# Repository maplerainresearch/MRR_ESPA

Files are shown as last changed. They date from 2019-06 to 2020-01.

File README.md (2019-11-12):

# MRR ESPA
## A basic 3D printer control board based on ESP32

This is a bare-minimum 3D printer control board based on the ESP32 microcontroller, which comes with built-in WiFi and BlueTooth.

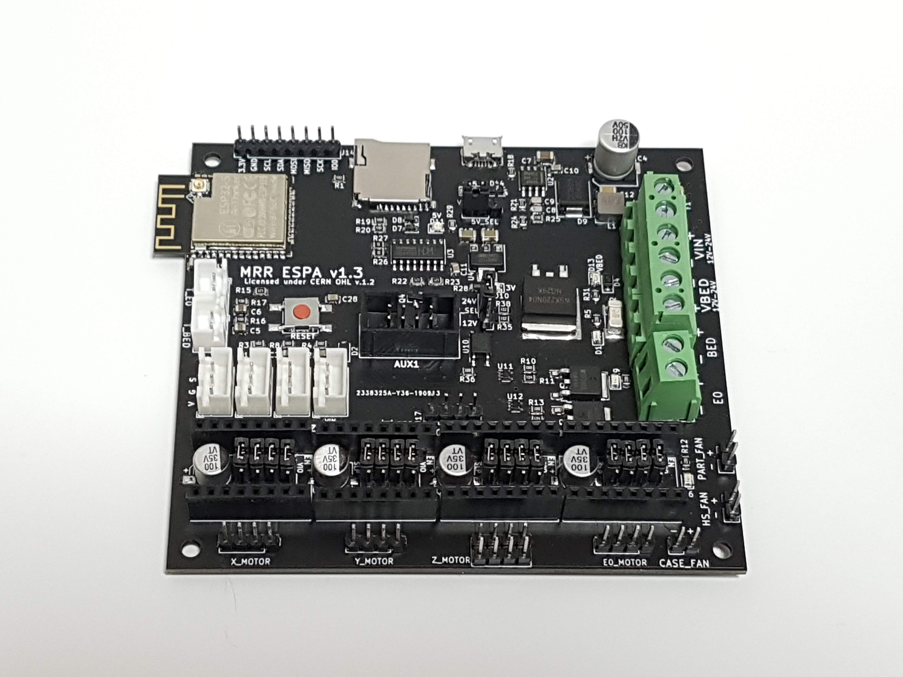
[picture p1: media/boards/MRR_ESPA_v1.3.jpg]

Current version: v1.3

Get a pre-launch version at our [store](https://www.maplerain.com/en/products).

Facebook [page](https://www.facebook.com/mrrespx/) <br>
Facebook [group](https://www.facebook.com/groups/mrr.espx.users/) (for discussions, etc.)

## Features:
- Able to use up to 4 stepper drivers: X, Y, Z, and E0
- 12V to 24V input power supply
- Separate power supply for the heat bed
- X, Y, and Z min endstops
- Allows the use of a Z-axis probe, such as an inductive sensor, running on the input supply voltage (12V to 24V)
- AUX1 connector for use with an external host, such as the closed-source MKS TFT32 (**Untested!!**)
- Physical size of 99.5mm by 90.5mm. Mounting holes are 3.5mm in diameter, with centers 4mm from the edges.
- "RESET" button can be used to reset the board.

(http://www.youtube.com/watch?v=s4IRmG6ibc4 "Basic features")

(http://www.youtube.com/watch?v=E-ERUolL-Bw "Printing via ESP3D webUI")

Check out the [Kickstarter page.](https://www.kickstarter.com/projects/maplerainresearch/mrr-espa)

# Firmware

Marlin 2.0 has added support for ESP32. This board was based on the initial pins definition used. <br>
In addition, [Luc](https://github.com/luc-github) has been working on a Marlin fork which incorporates part of his ESP3D webUI into Marlin itself.

## Flashing firmware

- You should be able to flash firmware through the USB port. Depending on your operating system, you may need to install drivers for the CH340. Please use Google or another search engine to find the right CH340 driver for your operating system.
- To flash firmware by directly connecting to TX/RX pins, you will need to connect IO0 to GND, then reboot (press "BOOT" button) to enter flash mode. After flashing the firmware, disconnect IO0 from GND, and press "BOOT" button again to reboot into normal mode.
- Use a baud rate of 115200.
- Once the firmware has been flashed for the first time, further updates can be flashed via OTA.

# Jumpers

- 5V_SEL: Connect to VIN for normal operation; only short (close) this jumper to VUSB if you need to power the board via USB. Note: Powering the board with both PSU and USB may cause unstable operation during heating.
- PWR_SEL: Connect the middle pin PWR_SEL to pin labeled "12V" if using 12V; connect PWR_SEL to pin labeled "24V" if using 24V.
- Stepper driver jumpers:
  - MS1: VIO to set high; SPI if using TMC SPI mode
  - MS2: VIO to set high; SPI if using TMC SPI mode
  - MS3: VIO to set high; SPI if using TMC SPI mode
  - RST: SLP if using A4988/DRV8825; SPI if using TMC SPI mode

# Pins

See separate PIN_DEF.txt file.

# License
Released under CERN Open Hardware Licence v1.2. See LICENSE.txt for details.

## Warning

- This product uses high currents which may cause fires. Use with caution.
- Do not use input voltages higher than 24V. Input current must not exceed 15A.
- Do not attempt to use more than 15A for the heated bed. While the MOSFET is capable of such currents, the connectors are not. If you need more than 15A, use an external MOSFET. In any case, it is highly recommended to use an external MOSFET for the heated bed to avoid drawing high currents through this product.
- If using a current of more than 10A for the heated bed, it is highly recommended to provide active cooling for the board as the MOSFET and adjacent areas can get very hot due to the high current.
- The underside of the board has PCB traces which are exposed for better cooling. These traces may be carrying high currents and can get very hot. DO NOT touch them, and DO NOT allow these traces to come into contact with metal or other conductive materials.
- Do not attempt to use more than 5A for the hot end. While the MOSFET is capable of such currents, the connectors are not. If you need more than 5A, use an external MOSFET.
- Do not reverse polarity.
- The breakout and endstop pins are rated for 3.3V, which is the voltage the ESP32 operates at. Attempting to feed inputs above 3.3V to these pins may damage the board.
- It is recommended to power the board only via USB (i.e. turn off PSU power supply) when flashing the board.

## Disclaimer

This product is provided as-is. While care has been taken to design a safe product, it is the user's responsibility to make sure precautions are taken to prevent damage or injury when using this product. This includes adhering to all warnings provided. By using this product, the user accepts responsibility to bear all liabilities from any damage or injury arising from the use of this product.

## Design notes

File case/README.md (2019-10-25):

# Cases for MRR ESPA

There are three versions:
1. Basic: Skeleton version, with a simple base, and a top that allows a 40mm fan to be fitted. Standoffs (at least 25mm; more if using stepper drivers with higher heat sinks) are needed.
2. Small: A small, almost enclosed case with a top that allows a 80mm fan to be fitted.
3. Normal: A slightly larger enclosed case, with two types of tops (either a 80mm fan, or two 40mm fans).

There are also covers for 40mm and 80mm fans.

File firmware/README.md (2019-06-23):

This directory contains ZIP files of firmware which works with the MRR ESP 3DP board.

MRR ESP 3DP board works with the [Marlin fork](https://github.com/luc-github/Marlin) currently under development by [Luc](https://github.com/luc-github). This fork provides WiFi support as well as a web UI based on Luc's [ESP3D](https://github.com/luc-github/ESP3D). Snapshots of the repo will be posted here. You can download the ZIP file, unpack it, and edit the Configuration.h and Configuration_adv.h to suit the size of your printer, drivers, etc. If you are using TMC2130 drivers in SPI mode, you will also need to edit pins_ESP32.h to specify the CS pins for the drivers. The fork has been tested to compile under Arduino IDE 1.8.5 using Arduino-ESP32 core v1.0.0 (stable release).

If you are using an external host such as the MKS TFT32 or Octoprint, you can also use vanilla Marlin 2.0, which has ESP32 support. However, this does not come with WiFi nor a web UI.

When flashing firmware, use a baud rate of 115200.

Default admin name and password:<br>
User: admin<br>
Password: admin<br>
<br>
Default general user name and password:<br>
User: user<br>
Password: user<br>

Default mDNS name: **marlinesp**, which can be accessed on web browsers by going to `http://marlinesp.local/`

For more about the web UI, see Luc's [ESP3D-WEBUI](https://github.com/luc-github/ESP3D-WEBUI) repository.

# Instructions for flashing firmware

The firmware is built on the Arduino framework with the ESP32 core from Espressif. If you have experience building and flashing firmware using the Arduino-ESP32 core, you probably do not need this guide and can easily flash the firmware using your usual method. Otherwise, you can follow the following to flash the firmware.

1. First, you need Arduino IDE installed on your computer (Windows, Mac, or Linux). Go to [Arduino IDE's download page](https://www.arduino.cc/en/main/software) to download the version of the IDE for your computer. Arduino IDE's installation guide can be found [here](https://www.arduino.cc/en/Guide/HomePage).

2. Once Arduino IDE has been installed, follow the instructions [here](https://github.com/espressif/arduino-esp32/blob/master/docs/arduino-ide/boards_manager.md) to install the ESP32 core for Arduino IDE. It is recommended to install the stable release.

3. Download or clone the [Marlin fork](https://github.com/luc-github/Marlin) currently under development by [Luc](https://github.com/luc-github).

4. Connect the board to your computer via USB cable.

5. Launch Arduino IDE, and open the sketch for the firmware. This file is named `Marlin.ino` and can be found in the downloaded firmware's `Marlin` subdirectory.

6. In the IDE's menu, go to `Tools`, then `Board`, and choose `ESP32 Dev Module` which is the generic ESP32 module. Then, under `Tools`, `Port`, choose the COM port that your board is connected to. For upload speed, go to `Tools`, `Upload speed`, and set to `115200`.

7. Edit the `Configuration.h` and `Configuration_adv.h` files to define the size of your printer, endstops, and other settings. See the section below for some basic settings which need to be changed.

8. Click on the "Upload" icon of the IDE to compile the firmware and flash it onto the board. This will take quite a while.

9. Once the firmware has been flashed onto the board, you can open the IDE's serial monitor (by pressing Ctrl+Shift+M, or from the menu via `Tools`, then `Serial monitor`) to make sure the firmware has been flashed properly. Enter `M503` into the serial monitor and you should get a response from the board giving the current settings such as steps/mm and PID values.

10. Via the serial monitor, you can configure your WiFi settings. See the section below on how to do so. You can also set up WiFi using a web browser (see relevant section below).

# Instructions for setting up WiFi via terminal

Once the firmware has been flashed for the first time, there is a need to do an initial setup for the WiFi settings.<br>
In Arduino IDE, open up the serial monitor to connect to the board. You can also use any other terminal program to open the COM port that the board is connected to. Then, type in the following commands 1 to 3 to set up the board in station mode (connect to an existing WiFi router). To set up in AP mode, use commands 1, 4, and 5.

1. `M586 P0 S1 R80`<br>
Enable HTTP on port 80.<br>
Replace `R80` with `Rxx` (xx is the port number) to run the HTTP server on another port.

2. `M587 S"abcd" P"12345" I192.168.0.25`<br>
WiFi settings; the above will connect to a SSID of `abcd` with password `12345` and attempt to use a static address of `192.168.0.25` (note: the quotation marks are necessary for SSID and password). Change `abcd`, `12345`, and `192.168.0.25` to your own values. `I192.168.0.25` can be left out if a static address is not needed.

3. `M588 S1 P1`<br>
This will start up WiFi in station mode, using the settings set by `M587`. The IP address of the webserver will be displayed in the terminal. Use this IP address to connect to the webserver. For example, going to `http://192.168.0.25:80/` on your web browser following the above example.

4. `M589 S"ESP32" P"12345" I192.168.10.1`<br>
WiFi settings; the above will create an access point with SSID of `ESP32` and password `12345`, and the webserver will be on IP address `192.168.10.1` (note: the quotation marks are necessary for SSID and password). WPA2 security will be used by default.

5. `M588 S2 P1`<br>
This will start up WiFi in AP mode, using the settings set by `M589`.

# Instructions for setting up WiFi via web browser

To be completed.

# Uploading webUI

When you first go to the webUI address (if you have mDNS, this should be http://marlinesp.local/ by default), you will be asked to upload the webUI files. Click on "Choose files", select `index.html.gz`, then upload. Then, refresh your browser page; the webUI should load. A copy of `index.html.gz` can be found in the firmware directory, under `<firmware directory>/Marlin/data/`.<br>

If you have the [Arduino ESP32 filesystem uploader](https://github.com/me-no-dev/arduino-esp32fs-plugin), you can also choose to upload the required files from Arduino IDE. After flashing the firmware, go to `Tools`, then choose `ESP32 Sketch Data Upload`.

# Common settings which need to be changed in Marlin

The following are some common settings which need to be changed in Marlin to configure the firmware for your specific printer.<br>

In `Configuration.h`:
To be completed.<br>

In `Configuration_adv.h`:
To be completed.<br>

In `Marlin\src\pins\pins_ESP32.h`:
The following lines need to be added in order for microSD card to work.<br>
```
#define MOSI_PIN           23
#define MISO_PIN           19
#define SCK_PIN            18
#define SS_PIN              5
#define SDSS                5
```

# Macros

The webUI (based on ESP3D) allows user-defined macros to be created. This allows "buttons" for custom commands (GCODE), such as buttons for babystepping.<br>

For example, to add a command to move to babystep Z by 0.01 downwards:
1. Create a text file with the gcode. In this case the gcode would be "M290 Z-0.01". Save it with a ".g" extension. In this case, it can be named `babyzdn.g`.
2. Upload that file to the ESP3D File System (Not to the SD card); this is the SPIFFS file system, where `index.html.gz` is stored.
3. Click on the macro editor button in the controls panel. click the plus icon to add a macro. Give it a name, select a color, set the target as ESP and enter the path to the gcode file you uploaded.
4. Click Save
(Example based on [GRBL_ESP32 wiki](https://github.com/bdring/Grbl_Esp32/wiki/ESP3D-Web-UI-for-Grbl_ESP32); GRBL_ESP32 is a fork of GRBL with luc-github's ESP3D webUI.)<br>

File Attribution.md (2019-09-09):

# Attribution

Schematics of the following boards were referenced in the design of MRR ESPA:
- [SMART RAMPS 1.42](https://reprap.org/wiki/SMART_RAMPS)
- [ESP32Controller](https://github.com/simon-jouet/ESP32Controller)
- [STEVAL-3DP001V1](https://www.st.com/en/evaluation-tools/steval-3dp001v1.html)
- [Duet 3D Printer Controller](https://github.com/T3P3/Duet)
- [Smoothieboard](https://github.com/Smoothieware/Smoothieboard)
- [Arduino UNO R3](https://www.arduino.cc/en/uploads/Main/Arduino_Uno_Rev3-schematic.pdf)
- [Little-Driver](https://github.com/Digital-Sqrt/Little-Driver)

Software:
- [Custom Marlin fork](https://github.com/luc-github/Marlin) by luc-github
- [ESP3D-WEBUI](https://github.com/luc-github/ESP3D-WEBUI)
- [Marlin firmware](https://github.com/MarlinFirmware/Marlin)

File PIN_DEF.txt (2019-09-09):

Pin Definitions for MRR ESPE
----------------------------

ESP32 pins
0: unused (IO0; must not be pulled low for normal bootup)
1: TX
2: HEATER_0_PIN
3: RX
4: HEATER_BED_PIN
5: SS_PIN (SDSS)
12: Z_DIR_PIN
13: FAN_PIN
14: Z_STEP_PIN
15: Z_MIN_PIN
16: E0_STEP_PIN
17: E0_DIR_PIN
18: SCK_PIN
19: MISO_PIN
21: unused (SDA)
22: unused (SCL)
23: MOSI_PIN
25: X_ENABLE_PIN (shared with Y, Z, and E0)
26: X_DIR_PIN
27: X_STEP_PIN
32: Y_DIR_PIN
33: Y_STEP_PIN
34: X_MIN_PIN
35: Y_MIN_PIN
36 (VP): TEMP_0_PIN
39 (VN): TEMP_BED_PIN

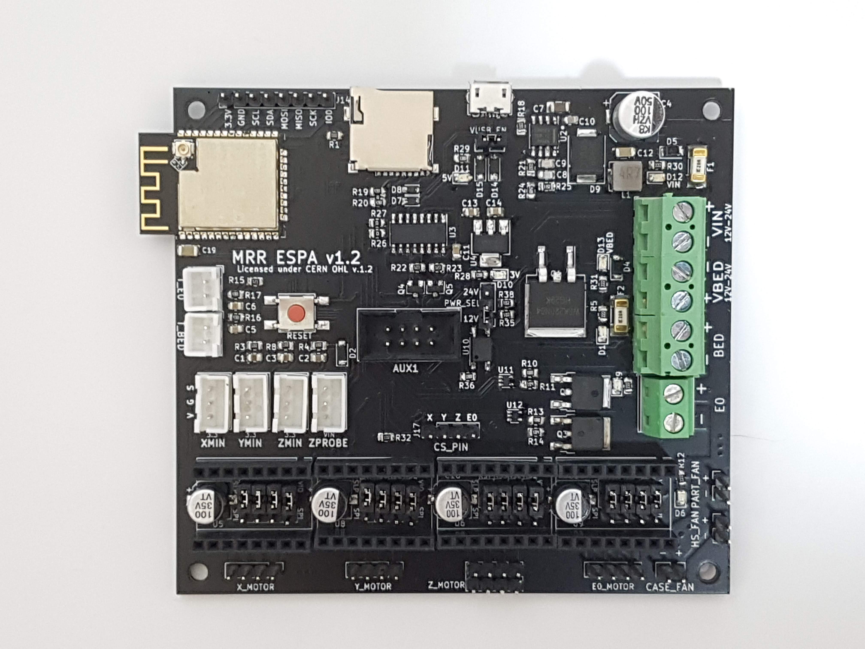
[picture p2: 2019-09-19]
media/ESPA board overview.jpg

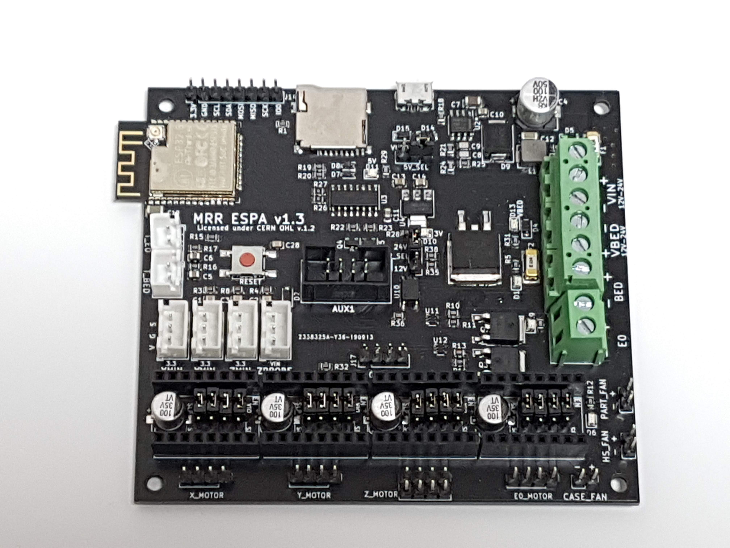
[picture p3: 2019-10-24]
media/MRR ESPA v1.3 board overview.jpg

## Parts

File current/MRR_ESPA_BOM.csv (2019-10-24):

Reference | Value | Footprint | Datasheet | LCSC Part Number | Manufacturer | Mfg part no.
U1 | ESP32-WROOM-32D | RF_Module:ESP32-WROOM-32 | https://www.espressif.com/sites/default/files/documentation/esp32-wroom-32d_esp32-wroom-32u_datasheet_en.pdf | C95209 | Espressif Systems | ESP32-WROOM-32
J9 | PWR_IN | TerminalBlock_Phoenix:TerminalBlock_Phoenix_MKDS-3-4-5.08_1x04_P5.08mm_Horizontal | ~ | C90087 | Phoenix Contact | MKDS3/4-5.08
F1 | 15A 2410 | projfp:Littelfuse_0451 | Bel 0679H9150-01 | C44480 | Littelfuse | 0451015.MRL
F2 | 30A 3912 | projfp:Littelfuse_456 | Bel 0678H9300-02 | C187558 | Littelfuse | 0456030.ER
D4 | 1N4007W | projfp:D_SOD-123F | http://www.vishay.com/docs/88503/1n4001.pdf | C108803 | Shandong Jingdao Microelectronics | 1N4007W
D5 | 1N4007W | projfp:D_SOD-123F | http://www.vishay.com/docs/88503/1n4001.pdf | C108803 | Shandong Jingdao Microelectronics | 1N4007W
U2 | TPS54340DDA | Package_SO:TI_SO-PowerPAD-8_ThermalVias | http://www.ti.com/lit/ds/symlink/tps54340.pdf | C45886 | Texas Instruments | TPS54340DDAR
C10 | 100nF50V | Capacitor_SMD:C_0805_2012Metric | ~ | C161260 | Murata Electronics | GCM21BR71H104KA37L
C7 | 4.7uF50V | Capacitor_SMD:C_1206_3216Metric | ~ | C307575 | Samsung Electro-Mechanics | CL31B475KBHNFNE
C4 | 100uF50V | Capacitor_SMD:CP_Elec_8x10 | ~ | C176665 | Lelon | VEJ101M1HTR-0810
L1 | 4.7uH4.5A | projfp:SMMS0530 | ~ | C181722 | Shun Xiang Nuo Elec | SMMS0530-4R7M
D9 | B540C-13-F | projfp:D_SMC | ~ | C72264 | Diodes Incorporated | B540C-13-F
R24 | 60.4K | Resistor_SMD:R_0805_2012Metric | ~ | C273994 | YAGEO | RC0805FR-0760K4L
R25 | 11.5K | Resistor_SMD:R_0805_2012Metric | ~ | C17418 | Uniroyal Elec | 0805W8F1152T5E
C12 | 47uF16V | Capacitor_SMD:C_1206_3216Metric | ~ | C92821 | Taiyo Yuden | LMK316BJ476ML-T
C8 | 820pF50V | Capacitor_SMD:C_0805_2012Metric | ~ | C152862 | Walsin Tech Corp | 0805B821K500CT
R21 | 23.7K | Resistor_SMD:R_0805_2012Metric | ~ | C170848 | Walsin Tech Corp | WR08X2372FTL
C9 | 56pF50V | Capacitor_SMD:C_0805_2012Metric | ~ | C296102 | Walsin Tech Corp | 0805N560J500CT
R18 | 73.2K | Resistor_SMD:R_0805_2012Metric | ~ | C170958 | Walsin Tech Corp | WR08X7322FTL
U4 | AMS1117-3.3 | Package_TO_SOT_SMD:SOT-223-3_TabPin2 | http://www.advanced-monolithic.com/pdf/ds1117.pdf | C6186 | Advanced Monolithic Systems | AMS1117-3.3
C14 | 47uF6.3V | Capacitor_SMD:C_0805_2012Metric | ~ | C87159 | Taiyo Yuden | JMK212BJ476MG-T
C13 | 47uF6.3V | Capacitor_SMD:C_0805_2012Metric | ~ | C87159 | Taiyo Yuden | JMK212BJ476MG-T
R28 | 220R | Resistor_SMD:R_0805_2012Metric | ~ | C17557 | Uniroyal Elec | 0805W8F2200T5E
D10 | LED_3V | projfp:LED_0805 | ~ | C73548 | Everlight Elec | 17-21SYGC/S530-E2/TR8
R29 | 330R | Resistor_SMD:R_0805_2012Metric | ~ | C17630 | Uniroyal Elec | 0805W8F3300T5E
R30 | 2.2K | Resistor_SMD:R_0805_2012Metric | ~ | C17520 | Uniroyal Elec | 0805W8F2201T5E
R31 | 2.2K | Resistor_SMD:R_0805_2012Metric | ~ | C17520 | Uniroyal Elec | 0805W8F2201T5E
D11 | LED_5V | projfp:LED_0805 | ~ | C73548 | Everlight Elec | 17-21SYGC/S530-E2/TR8
D12 | LED_VIN | projfp:LED_0805 | ~ | C72035 | Everlight Elec | 17-21/BHC-XL2M2TY/3T
D13 | LED_VBED | projfp:LED_0805 | ~ | C72035 | Everlight Elec | 17-21/BHC-XL2M2TY/3T
R26 | 0R | Resistor_SMD:R_0805_2012Metric | ~ | C17477 | Uniroyal Elec | 0805W8F0000T5E
R27 | 0R | Resistor_SMD:R_0805_2012Metric | ~ | C17477 | Uniroyal Elec | 0805W8F0000T5E
C11 | 10nF50V | Capacitor_SMD:C_0805_2012Metric | ~ | C52278 | Guangdong Fenghua Advanced Tech | 0805B103K500NT
J16 | USB_B_Micro | Connector_USB:USB_Micro-B_Molex-105017-0001 | ~ | C136000 | MOLEX | 105017-0001
D7 | PESD5V0S1BA | projfp:D_SOD-323 | ~ | C19224 | Nexperia | PESD5V0S1BA,115
D8 | PESD5V0S1BA | projfp:D_SOD-323 | ~ | C19224 | Nexperia | PESD5V0S1BA,115
Q4 | S9014 | Package_TO_SOT_SMD:SOT-23 | http://www.onsemi.com/pub_link/Collateral/2N3055-D.PDF | C181164 | Guangdong Hottech | S9014
Q5 | S9014 | Package_TO_SOT_SMD:SOT-23 | http://www.onsemi.com/pub_link/Collateral/2N3055-D.PDF | C181164 | Guangdong Hottech | S9014
R22 | 12K | Resistor_SMD:R_0805_2012Metric | ~ | C17444 | Uniroyal Elec | 0805W8F1202T5E
R23 | 12K | Resistor_SMD:R_0805_2012Metric | ~ | C17444 | Uniroyal Elec | 0805W8F1202T5E
Q1 | WSK220N04 | Package_TO_SOT_SMD:TO-263-2 | ~ | C148446 | Winsok Semicon | WSK220N04
Q2 | WSF3085 | Package_TO_SOT_SMD:TO-252-2 | ~ | C148428 | Winsok Semicon | WSF3085
Q3 | WSF3038 | Package_TO_SOT_SMD:TO-252-2 | ~ | C148426 | Winsok Semicon | WSF3038
R5 | 2.2K | Resistor_SMD:R_0805_2012Metric | ~ | C17520 | Uniroyal Elec | 0805W8F2201T5E
D1 | LED_BED | projfp:LED_0805 | ~ | C72037 | Everlight Elec | 17-21SURC/S530-A3/TR8
J3 | BED | TerminalBlock_Phoenix:TerminalBlock_Phoenix_MKDS-3-2-5.08_1x02_P5.08mm_Horizontal | ~ | C89120 | Phoenix Contact | MKDS3/2-5.08
R9 | 2.2K | Resistor_SMD:R_0805_2012Metric | ~ | C17520 | Uniroyal Elec | 0805W8F2201T5E
J7 | E0 | TerminalBlock_Phoenix:TerminalBlock_Phoenix_MKDS-1,5-2-5.08_1x02_P5.08mm_Horizontal | ~ | C91153 | Phoenix Contact | MKDSN1.5/2-5.08
R10 | 10R | Resistor_SMD:R_0805_2012Metric | ~ | C17415 | Uniroyal Elec | 0805W8F100JT5E
R11 | 100K | Resistor_SMD:R_0805_2012Metric | ~ | C149504 | Uniroyal Elec | 0805W8F1003T5E
R12 | 2.2K | Resistor_SMD:R_0805_2012Metric | ~ | C17520 | Uniroyal Elec | 0805W8F2201T5E
R13 | 10R | Resistor_SMD:R_0805_2012Metric | ~ | C17415 | Uniroyal Elec | 0805W8F100JT5E
R14 | 100K | Resistor_SMD:R_0805_2012Metric | ~ | C149504 | Uniroyal Elec | 0805W8F1003T5E
J10 | PART_FAN | Connector_PinHeader_2.54mm:PinHeader_1x02_P2.54mm_Vertical | ~ | C124375 | Shenzhen Cankemeng | C124375
U8 | Pololu_board | Module:Pololu_Breakout-16_15.2x20.3mm |  | C27438 | Boom Precision Elec | x2
U5 | Pololu_board | Module:Pololu_Breakout-16_15.2x20.3mm |  | C27438 | Boom Precision Elec | x2
J21 | X_MOTOR | Connector_PinHeader_2.54mm:PinHeader_1x04_P2.54mm_Vertical | ~ | C124378 | Shenzhen Cankemeng | C124378
C15 | 100uF35V | Capacitor_SMD:CP_Elec_6.3x7.7 | ~ | C97811 | Semtech | CS1V101M-CRE77
U6 | Pololu_board | Module:Pololu_Breakout-16_15.2x20.3mm |  | C27438 | Boom Precision Elec | x2
U9 | Pololu_board | Module:Pololu_Breakout-16_15.2x20.3mm |  | C27438 | Boom Precision Elec | x2
R32 | 10K | Resistor_SMD:R_0805_2012Metric | ~ | C38522 | Uniroyal Elec | 0805W8F2201T5E
J11 | FAN_HEATSINK | Connector_PinHeader_2.54mm:PinHeader_1x02_P2.54mm_Vertical | ~ | C124375 | Shenzhen Cankemeng | C124375
C16 | 100uF35V | Capacitor_SMD:CP_Elec_6.3x7.7 | ~ | C97811 | Semtech | CS1V101M-CRE77
C17 | 100uF35V | Capacitor_SMD:CP_Elec_6.3x7.7 | ~ | C97811 | Semtech | CS1V101M-CRE77
C18 | 100uF35V | Capacitor_SMD:CP_Elec_6.3x7.7 | ~ | C97811 | Semtech | CS1V101M-CRE77
J23 | Y_MOTOR | Connector_PinHeader_2.54mm:PinHeader_1x04_P2.54mm_Vertical | ~ | C124378 | Shenzhen Cankemeng | C124378
J24 | E0_MOTOR | Connector_PinHeader_2.54mm:PinHeader_1x04_P2.54mm_Vertical | ~ | C124378 | Shenzhen Cankemeng | C124378
J22 | Z_MOTOR | Connector_PinHeader_2.54mm:PinHeader_2x04_P2.54mm_Vertical | ~ | C124386 | Shenzhen Cankemeng | C124386
D3 | LED_E0 | projfp:LED_0805 | ~ | C72037 | Everlight Elec | 17-21SURC/S530-A3/TR8
D6 | LED_FAN | projfp:LED_0805 | ~ | C72037 | Everlight Elec | 17-21SURC/S530-A3/TR8
J8 | FAN_CASE | Connector_PinHeader_2.54mm:PinHeader_1x02_P2.54mm_Vertical | ~ | C124375 | Shenzhen Cankemeng | C124375
J12 | T_BED | Connector_JST:JST_XH_B02B-XH-A_1x02_P2.50mm_Vertical | ~ | C158012 | JST Sales America | B2B-XH-A(LF)(SN)
R16 | 4.7K | Resistor_SMD:R_0805_2012Metric | ~ | C17673 | Uniroyal Elec | 0805W8F4701T5E
C5 | 22uF6.3V | Capacitor_SMD:C_0805_2012Metric | ~ | C5674 | Samsung Electro-Mechanics | CL21A226MQQNNNE
J13 | T_E0 | Connector_JST:JST_XH_B02B-XH-A_1x02_P2.50mm_Vertical | ~ | C158012 | JST Sales America | B2B-XH-A(LF)(SN)
R17 | 4.7K | Resistor_SMD:R_0805_2012Metric | ~ | C17673 | Uniroyal Elec | 0805W8F4701T5E
C6 | 22uF6.3V | Capacitor_SMD:C_0805_2012Metric | ~ | C5674 | Samsung Electro-Mechanics | CL21A226MQQNNNE
J1 | X_MIN | Connector_JST:JST_XH_B03B-XH-A_1x03_P2.50mm_Vertical | ~ | C144394 | JST Sales America | B3B-XH-A(LF)(SN)
R3 | 10K | Resistor_SMD:R_0805_2012Metric | ~ | C38522 | Uniroyal Elec | 0805W8F2201T5E
C1 | 100nF25V | Capacitor_SMD:C_0805_2012Metric | ~ | C128353 | Walsin Tech Corp | 0805B104K250
J5 | Y_MIN | Connector_JST:JST_XH_B03B-XH-A_1x03_P2.50mm_Vertical | ~ | C144394 | JST Sales America | B3B-XH-A(LF)(SN)
R8 | 10K | Resistor_SMD:R_0805_2012Metric | ~ | C38522 | Uniroyal Elec | 0805W8F2201T5E
C3 | 100nF25V | Capacitor_SMD:C_0805_2012Metric | ~ | C128353 | Walsin Tech Corp | 0805B104K250
J2 | Z_MIN | Connector_JST:JST_XH_B03B-XH-A_1x03_P2.50mm_Vertical | ~ | C144394 | JST Sales America | B3B-XH-A(LF)(SN)
R4 | 10K | Resistor_SMD:R_0805_2012Metric | ~ | C38522 | Uniroyal Elec | 0805W8F2201T5E
C2 | 100nF25V | Capacitor_SMD:C_0805_2012Metric | ~ | C128353 | Walsin Tech Corp | 0805B104K250
J6 | Z_PROBE | Connector_JST:JST_XH_B03B-XH-A_1x03_P2.50mm_Vertical | ~ | C144394 | JST Sales America | B3B-XH-A(LF)(SN)
D2 | 1N4148W | projfp:D_SOD-123 | https://www.vishay.com/docs/85748/1n4148w.pdf | C81598 | Semtech | 1N4148W
R15 | 12K | Resistor_SMD:R_0805_2012Metric | ~ | C17444 | Uniroyal Elec | 0805W8F1202T5E
SW1 | RESET | projfp:6x6mmTactileSwitch |  | C83206 | Korean Hroparts Elec | K2-6639SP-C4SC-04
J15 | AUX1 | Connector_IDC:IDC-Header_2x04_P2.54mm_Vertical | ~ | C9135 | Boom Precision Elec | C9135
J14 | I2C/SPI | Connector_PinHeader_2.54mm:PinHeader_1x08_P2.54mm_Vertical | ~ | C124381 | Shenzhen Cankemeng | C124381
R19 | 4.7K | Resistor_SMD:R_0805_2012Metric | ~ | C17673 | Uniroyal Elec | 0805W8F4701T5E
R20 | 4.7K | Resistor_SMD:R_0805_2012Metric | ~ | C17673 | Uniroyal Elec | 0805W8F4701T5E
H1 | MountingHole | MountingHole:MountingHole_3.2mm_M3_DIN965 | ~
H2 | MountingHole | MountingHole:MountingHole_3.2mm_M3_DIN965 | ~
H3 | MountingHole | MountingHole:MountingHole_3.2mm_M3_DIN965 | ~
H4 | MountingHole | MountingHole:MountingHole_3.2mm_M3_DIN965 | ~
JP1 | X_MS1 | Connector_PinHeader_2.54mm:PinHeader_1x03_P2.54mm_Vertical | ~ | C124376 | Shenzhen Cankemeng | C124376
JP5 | X_MS2 | Connector_PinHeader_2.54mm:PinHeader_1x03_P2.54mm_Vertical | ~ | C124376 | Shenzhen Cankemeng | C124376
JP9 | X_MS3 | Connector_PinHeader_2.54mm:PinHeader_1x03_P2.54mm_Vertical | ~ | C124376 | Shenzhen Cankemeng | C124376
JP13 | X_RST | Connector_PinHeader_2.54mm:PinHeader_1x03_P2.54mm_Vertical | ~ | C124376 | Shenzhen Cankemeng | C124376
JP2 | Y_MS1 | Connector_PinHeader_2.54mm:PinHeader_1x03_P2.54mm_Vertical | ~ | C124376 | Shenzhen Cankemeng | C124376
JP6 | Y_MS2 | Connector_PinHeader_2.54mm:PinHeader_1x03_P2.54mm_Vertical | ~ | C124376 | Shenzhen Cankemeng | C124376
JP10 | Y_MS3 | Connector_PinHeader_2.54mm:PinHeader_1x03_P2.54mm_Vertical | ~ | C124376 | Shenzhen Cankemeng | C124376
JP14 | Y_RST | Connector_PinHeader_2.54mm:PinHeader_1x03_P2.54mm_Vertical | ~ | C124376 | Shenzhen Cankemeng | C124376
JP3 | Z_MS1 | Connector_PinHeader_2.54mm:PinHeader_1x03_P2.54mm_Vertical | ~ | C124376 | Shenzhen Cankemeng | C124376
JP7 | Z_MS2 | Connector_PinHeader_2.54mm:PinHeader_1x03_P2.54mm_Vertical | ~ | C124376 | Shenzhen Cankemeng | C124376
JP11 | Z_MS3 | Connector_PinHeader_2.54mm:PinHeader_1x03_P2.54mm_Vertical | ~ | C124376 | Shenzhen Cankemeng | C124376
JP15 | Z_RST | Connector_PinHeader_2.54mm:PinHeader_1x03_P2.54mm_Vertical | ~ | C124376 | Shenzhen Cankemeng | C124376
JP4 | E0_MS1 | Connector_PinHeader_2.54mm:PinHeader_1x03_P2.54mm_Vertical | ~ | C124376 | Shenzhen Cankemeng | C124376
JP8 | E0_MS2 | Connector_PinHeader_2.54mm:PinHeader_1x03_P2.54mm_Vertical | ~ | C124376 | Shenzhen Cankemeng | C124376
JP12 | E0_MS3 | Connector_PinHeader_2.54mm:PinHeader_1x03_P2.54mm_Vertical | ~ | C124376 | Shenzhen Cankemeng | C124376
JP16 | E0_RST | Connector_PinHeader_2.54mm:PinHeader_1x03_P2.54mm_Vertical | ~ | C124376 | Shenzhen Cankemeng | C124376
U3 | CH340C | Package_SO:SOIC-16_3.9x9.9mm_P1.27mm | http://www.datasheet5.com/pdf-local-2195953 | C84681 | Jiangsu Qin Heng | CH340C
J4 | Micro_SD_Card_China | projfp:Conn_uSDcard |  | C111196 | SOFNG | TF-15×15
C19 | 100uF6.3V | Capacitor_SMD:C_1206_3216Metric | ~ | C15008 | Samsung Electro-Mechanics | CL31A107MQHNNNE
R38 | 1K | Resistor_SMD:R_0805_2012Metric | ~ | C17513 | Uniroyal Elec | 0805W8F1001T5E
R35 | 1K | Resistor_SMD:R_0805_2012Metric | ~ | C17513 | Uniroyal Elec | 0805W8F1001T5E
U10 | TLP182 | Package_SO:MFSOP6-4_4.4x3.6mm_P1.27mm | https://toshiba.semicon-storage.com/info/docget.jsp?did=11793&prodName=TLP184 | C96457 | TOSHIBA | TLP182(GB-TPL,E
U11 | 74LVC1G125 | Package_TO_SOT_SMD:SOT-353_SC-70-5 | http://www.ti.com/lit/sg/scyt129e/scyt129e.pdf | C12519 | Nexperia | 74LVC1G125GW,125
U12 | 74LVC1G125 | Package_TO_SOT_SMD:SOT-353_SC-70-5 | http://www.ti.com/lit/sg/scyt129e/scyt129e.pdf | C12519 | Nexperia | 74LVC1G125GW,125
R36 | 330R | Resistor_SMD:R_0805_2012Metric | ~ | C17630 | Uniroyal Elec | 0805W8F3300T5E
D14 | 1N5819W | Diode_SMD:D_SOD-123 | http://www.vishay.com/docs/88525/1n5817.pdf | C169540 | Shandong Jingdao Microelectronics | 1N5819W
D15 | 1N5819W | Diode_SMD:D_SOD-123 | http://www.vishay.com/docs/88525/1n5817.pdf | C169540 | Shandong Jingdao Microelectronics | 1N5819W
J17 | CS_PINS | Connector_PinHeader_2.54mm:PinHeader_1x04_P2.54mm_Vertical | ~ | C124378 | Shenzhen Cankemeng | C124378
R1 | 10K | Resistor_SMD:R_0805_2012Metric | ~ | C38522 | Uniroyal Elec | 0805W8F2201T5E
JP18 | PWR_SEL | Connector_PinHeader_2.54mm:PinHeader_1x03_P2.54mm_Vertical | ~ | C124376 | Shenzhen Cankemeng | C124376
JP17 | 5V_SEL | Connector_PinHeader_2.54mm:PinHeader_1x03_P2.54mm_Vertical | ~ | C124376 | Shenzhen Cankemeng | C124376
C28 | 100nF25V | Capacitor_SMD:C_0805_2012Metric | ~ | C128353 | Walsin Tech Corp | 0805B104K250

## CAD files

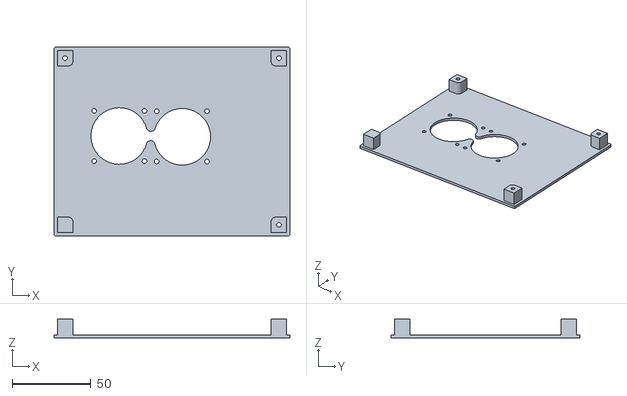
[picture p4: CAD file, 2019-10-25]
case/ESPA_top_40mm_fan.stl
150.0 x 120.0 x 12.0

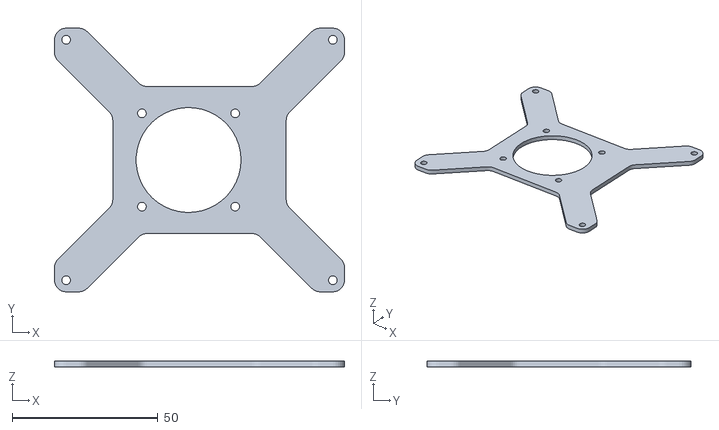
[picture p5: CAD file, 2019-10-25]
case/ESPA_basic_top_40mm.stl
99.5 x 90.5 x 2.00

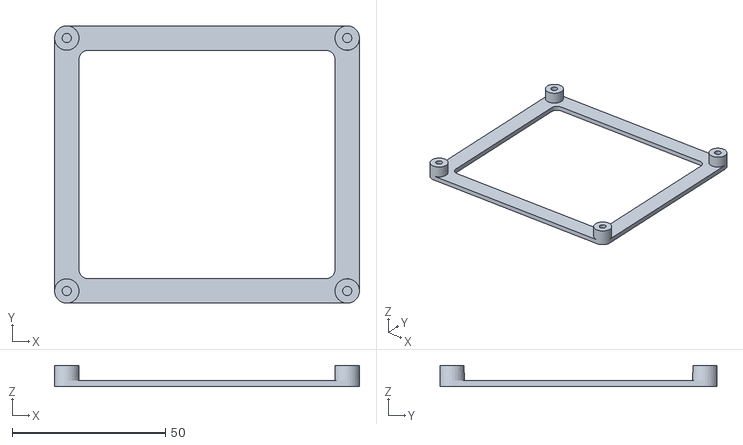
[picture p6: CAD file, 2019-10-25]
case/ESPA_basic_bottom.stl
99.5 x 90.5 x 7.00

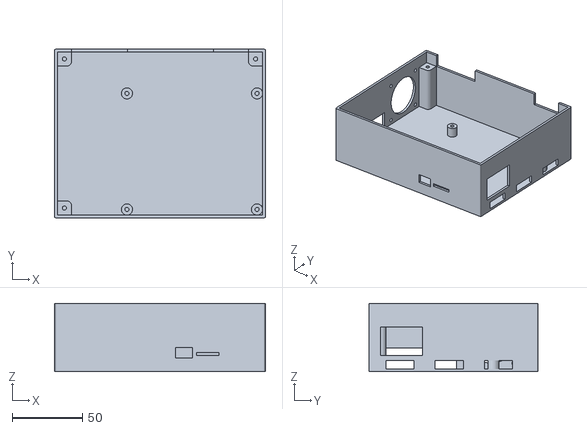
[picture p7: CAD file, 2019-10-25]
case/ESPA_bottom.stl
150.0 x 120.0 x 48.6

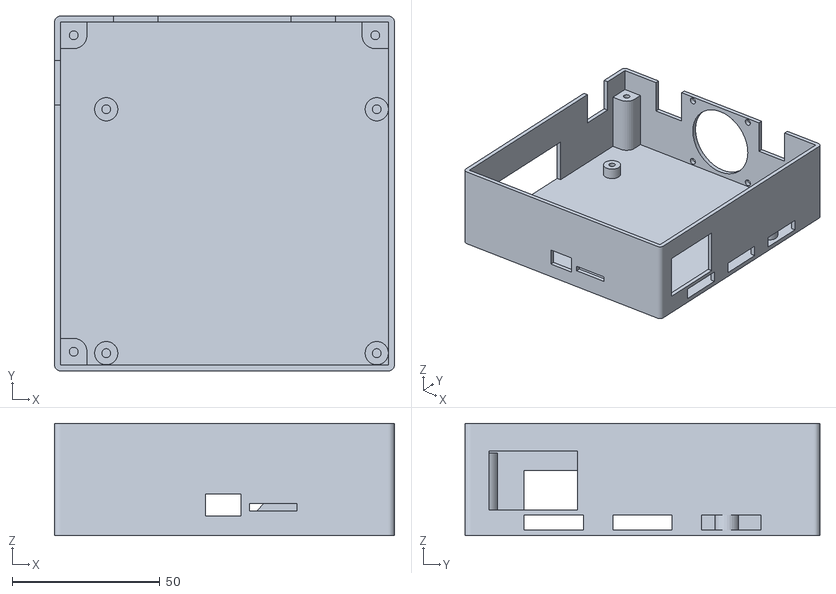
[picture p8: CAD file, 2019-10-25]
case/ESPA_bottom_small.stl
115.0 x 120.0 x 38.0

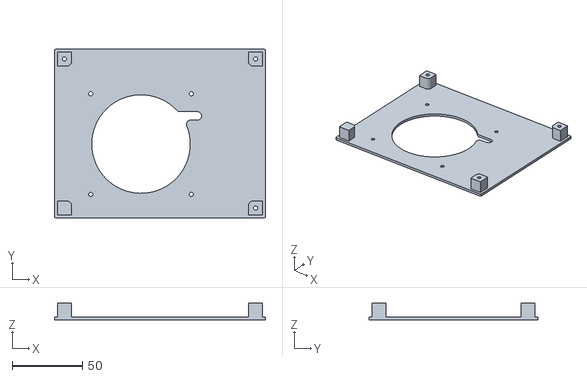
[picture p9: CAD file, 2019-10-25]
case/ESPA_top_80mm_fan.stl
150.0 x 120.0 x 12.0

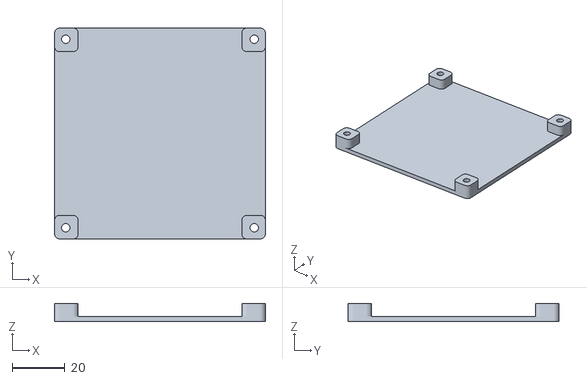
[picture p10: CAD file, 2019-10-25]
case/80mm_fan_cover.stl
80.0 x 80.0 x 7.00

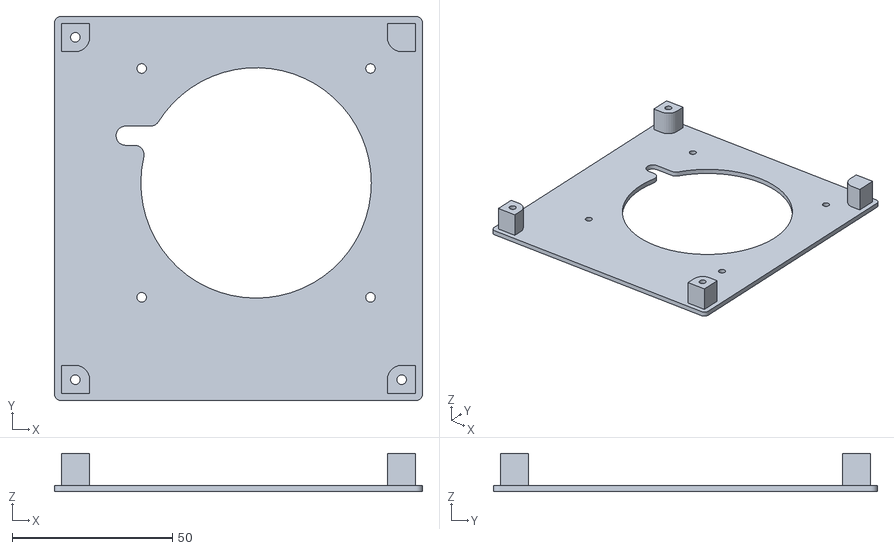
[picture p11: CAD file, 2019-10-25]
case/ESPA_top_small_80mm_fan.stl
115.0 x 120.0 x 12.0

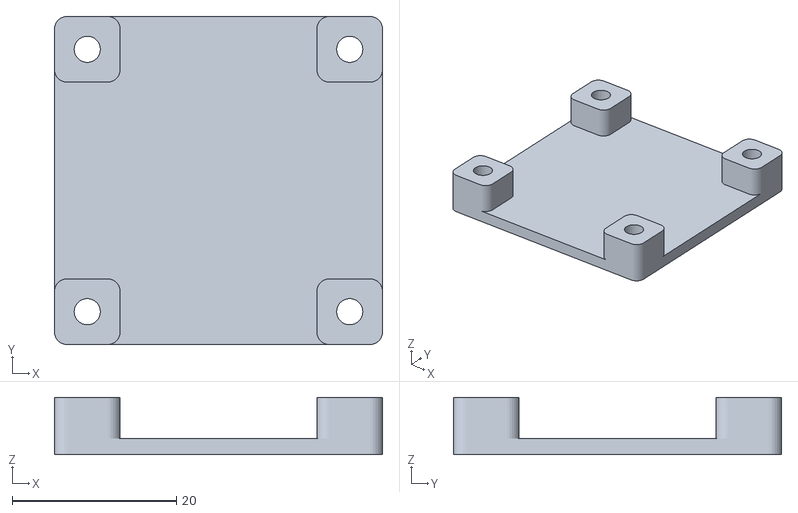
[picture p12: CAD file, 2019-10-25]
case/40mm_fan_cover.stl
40.0 x 40.0 x 7.00

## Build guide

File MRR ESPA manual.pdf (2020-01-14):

# MRR ESPA

# Version 1.3

# Getting Started

Document version: 1.1
Document date: January 14, 2020

Copyright 2020 Maple Rain Research Co., Ltd.

## Contents

### Features

The MRR ESPA is a 32-bit 3D printer control board using an ESP32 microcontroller. Besides interpreting G-codes for 3D printing, the ESP32 microcontroller acts as a web server that provides a web interface for controlling the printer. The board comes with the following features: - Able to use up to 4 stepper drivers—X, Y, Z, and E0—and also allowing up to 2

motors to be connected in parallel for Z axis. - 12V to 24V input power supply

- Allows separate power supply to be used for the heated bed through use of an optocoupler - X, Y, and Z min endstops - Allows the use of a Z-axis probe, such as an inductive sensor, running on the input

supply voltage (12V to 24V) - AUX1 connector for use with an external host, such as the closed-source MKS TFT32

- Web interface over 802.11 b/g/n Wi-Fi (implemented via firmware)

Specifications (ESP32 microcontroller) - Tensilica Xtensa 32-bit LX6 microprocessor with dual cores - Clock frequency up to 240 MHz

- 802.11 b/g/n Wi-Fi supporting WFA, WPA/WPA2 and WAPI - Bluetooth v4.2 BR/EDR and Bluetooth Low Energy (BLE) - ROM: 448 KB
- SRAM: 520 KB
- Flash memory: 4 MB
- Peripheral input/output: ADC, DAC, I²C, UART, CAN 2.0, SPI, I²S, RMII, PWM, and more.

### Board Layout

Physical dimensions - 99.5 mm by 90.5 mm

- M3 mounting holes at each corner. Center of mounting hole is 4 mm from the edges of the board. - Board thickness: 1.6 mm

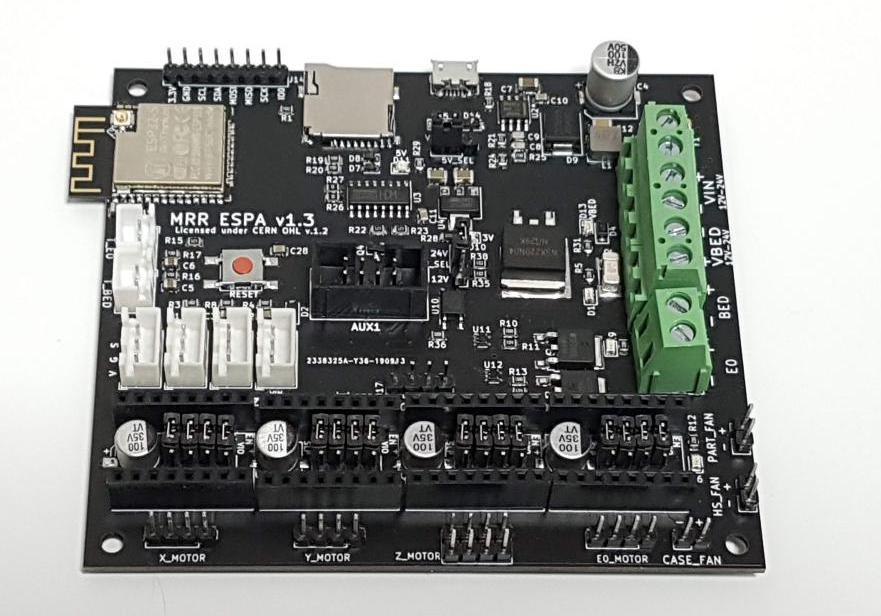
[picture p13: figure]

### Connectors

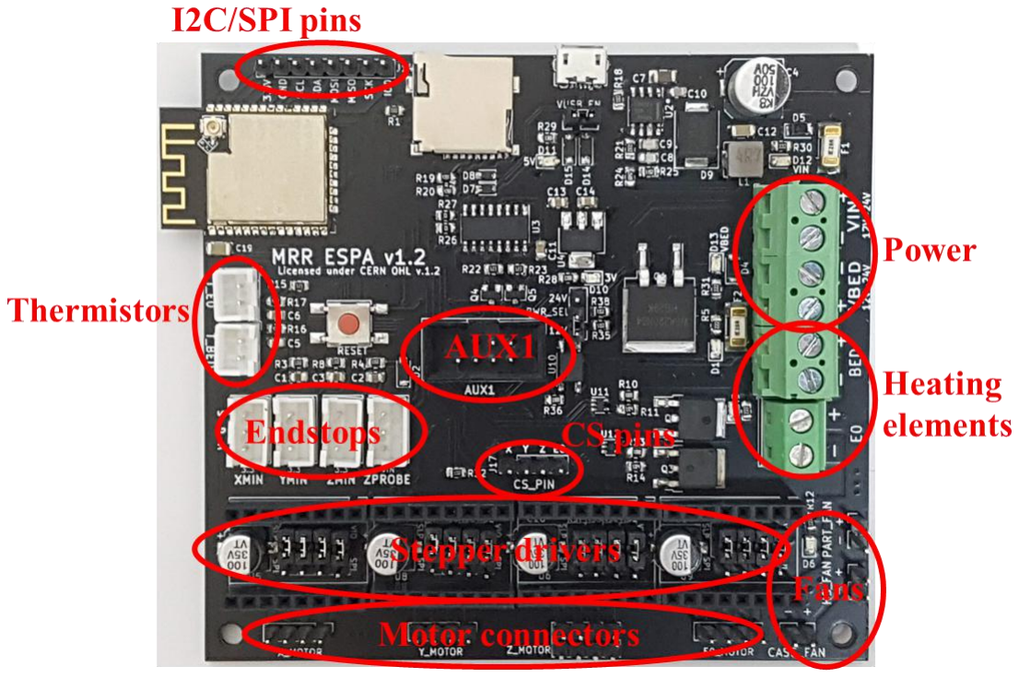
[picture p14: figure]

Power
VIN:- Main power supply for the MRR ESPA. - Accepts supply voltage from 12V to 24V. - Used to power all devices connected to the MRR ESPA, except the heated bed. This

includes the hot end heating block, motors, and fans. - Maximum current allowed is 10A. VBED: - Power supply for the heated bed. - Accepts supply voltage from 12V to 24V. - Maximum current allowed is 15A. Heating elements

BED: - For connecting to a heated bed. - Maximum current allowed is 15A. E0: - For connecting to the hot end heating block.

- Maximum current allowed is 5A. Fans

PART_FAN: - Connector for part cooling fan. - Use a fan rated for a voltage that matches the voltage of VIN. - Can be controlled by firmware. HS_FAN: - Connector for hot end’s heatsink cooling fan. - Use a fan rated for a voltage that matches the voltage of VIN. - Always on; cannot be controlled via firmware. CASE_FAN: - Connector for case fan. - Use a fan rated for a voltage that matches the voltage of VIN. - Always on; cannot be controlled by firmware. Thermistors

T_BED: - Thermistor for heated bed. T_E0: - Thermistor for hot end. Endstops

X_MIN: - X minimum endstop. - Externally pulled high to 3.3V. Y_MIN: - Y minimum endstop. - Externally pulled high to 3.3V. Z_MIN: - Z minimum endstop. - Externally pulled high to 3.3V. ZPROBE: - For connecting to a capacitive or inductive probe instead of a mechanical switch for

the Z minimum endstop. - The probe will be supplied with the same voltage as VIN. Please make sure that the

connected probe is rated for this voltage.

Stepper drivers - There are four sets of connectors for four stepper drivers. - Note the orientation of the stepper driver. The EN pin on the stepper driver should be

in the row away from the edge of the board. Motors

X_MOTOR: - For connecting to the X-axis stepper motor. Y_MOTOR: - For connecting to the Y-axis stepper motor. Z_MOTOR: - For connecting to the Z-axis stepper motor. E0_MOTOR: - For connecting to the extruder stepper motor. Others

AUX1: - For connecting to an external host controller like the MKS TFT32 using UART. - Supply voltage on this connector is 5V. I2C/SPI: - Breakout headers for I2C and SPI pins. - GPIO 0 (IO0) is also available for troubleshooting purposes. Connect GPIO 0 to

ground, then boot/reset the board to manually enter flash mode. USB: - For connecting to an external host computer. - When connected to a host computer, a serial terminal can be used to send gcodes to

the MRR ESPA. MicroSD: - For use with a microSD card. - The microcontroller can work with partitions up to 4 GB in size. - There is no automatic detection of microSD card. Each time a card is inserted, the

MRR ESPA needs to be informed via the gcode M21.

### Jumpers

USB power
5V_SEL: - Allows the board to be powered via USB or VIN. - This jumper should usually be connected to VIN. - Connect this jumper to VUSB only when flashing the firmware, or when you need to

power the board via USB. Note: Powering the board via USB while heating the heated bed can cause unstable operation. Bed MOSFET signal voltage

PWR_SEL: - Allows the bed MOSFET’s gate to be powered by a higher voltage so as to reduce

RDS(on). - When powered using 12V to 18V for VBED, set the jumper to connect the middle pin

with the pin labeled “12V”. - When powered by a voltage above 18V for VBED, set the jumper to connect the

middle pin with the pin labeled “24V”.

Stepper motor drivers

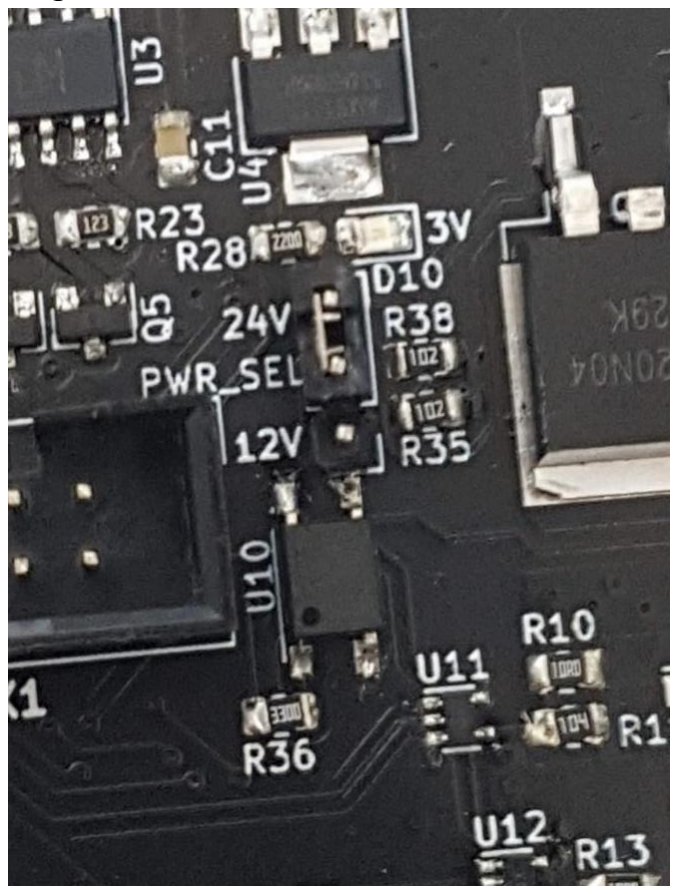
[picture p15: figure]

MS1: - Connect to VIO to set MS1 to high for microstepping; connect to SPI side to enable

SPI mode for Trinamic drivers.

MS2: - Connect to VIO to set MS2 to high for microstepping; connect to SPI side to enable

SPI mode for Trinamic drivers. MS3: - Connect to VIO to set MS3 to high for microstepping; connect to SPI side to enable

SPI mode for Trinamic drivers. RST:- Connect to SLP if using A4988 or DRV8825 drivers, or if using Trinamic drivers in

standalone mode; connect to SPI side to enable SPI mode for Trinamic drivers.

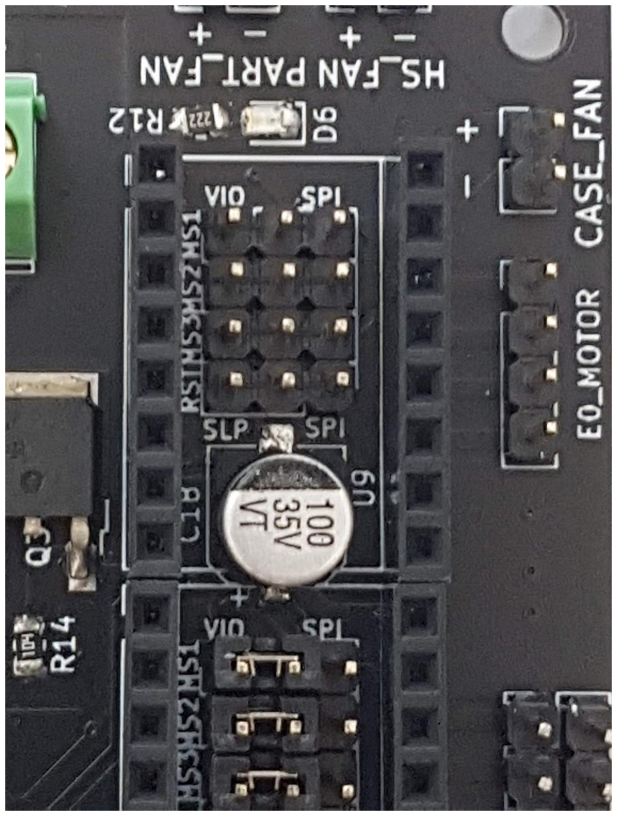
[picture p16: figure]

### Connecting the board

Endstops: - Connect the cables for the X, Y, and Z minimum endstops to the board’s XMIN, YMIN, and ZMIN respectively. - Note the polarity: V for 3.3V, G for ground, and S for signal. Probe: - If using a Z probe, such as an inductive probe, connect the probe’s cable to ZPROBE

instead of ZMIN. - Note the polarity: V for 12V to 24V (depends on VIN voltage), G for ground, and S

for signal. Connecting the probe wrongly may damage the probe. Thermistors: - Connect the hotend thermistor to T_E0. - If using a heated bed, connect the heated bed thermistor to T_BED. Stepper drivers and motors: - Set the jumpers for each stepper driver to the required microstepping (if using A4988, DRV8825, or Trinamic steppers in standalone mode) or to the SPI side (if using

Trinamic steppers in SPI mode). - Place the stepper drivers for each motor (X, Y, Z, E0) into the set of connectors

corresponding to their motor connectors. - Note the orientation of the stepper driver. The EN pin on the stepper driver should be

in the row away from the edge of the board. Placing the stepper driver in the wrong orientation can damage the stepper driver. - Connect the cables from the X, Y, Z, and extruder motors to X_MOTOR, Y_MOTOR, Z_MOTOR, and E0_MOTOR on the board respectively. - For Z axis, 2 motors can be connected in parallel. Fans:- Connect the case fan (for cooling the control board) to CASE_FAN. - Connect the hotend heatsink cooling fan (which is always on) to HS_FAN. - Connect the part cooling fan (controlled by gcode) to PART_FAN. - Note the polarity; usually, the red or yellow wire is positive (+), and the black or blue

wire is negative (-). Reversing polarity may damage the fan. Hotend: - Connect the cable for the hotend’s heating cartridge to E0.

- Polarity matters if you are connecting this to an external MOSFET. Heated bed: - If using a heated bed, connect the cable for the heated bed to BED. - Polarity matters if you are connecting this to an external MOSFET. Main power supply: - Connect the board’s power supply (12V to 24V) to VIN. - Note the polarity; the positive wire (usually red) should go to +, while the ground

wire (usually black) goes to -. Reversing polarity can damage the board and render it unusable. It may also damage the hotend MOSFET, causing the hotend to heat up uncontrollably when power is turned on. This may become a potential fire hazard. Heated bed power supply: - Connect the power supply for the heated bed (12V to 24V) to VBED. A separate

power supply from VIN can be used as the heated bed is controlled via an optocoupler. - Note the polarity; the positive wire (usually red) should go to +, while the ground

wire (usually black) goes to -. Reversing polarity can damage the board and cause the bed to heat up uncontrollably when power is turned on. This may become a potential fire hazard. - Set the PWR_SEL jumper according to the voltage being used for VBED: when using

12V to 18V for VBED, set the jumper to connect the middle pin with the pin labeled “12V”; when using a voltage above 18V for VBED, set the jumper to connect the middle pin with the pin labeled “24V”. External host: - An external host controller, such as the MKS TFT32, can be connected to AUX1.

### Setting Up the Firmware

The board is sold without the firmware being flashed. Therefore, when using it for the first time, the firmware must be configured and flashed. Flashing firmware

- Download | a | copy | of | the | firmware, | such | as | from
https://github.com/maplerainresearch/Marlin or the main Marlin repository at https://github.com/MarlinFirmware/Marlin.If this is downloaded as a ZIP file, it will need to be uncompressed to a directory on your local hard drive. - Connect the board via USB to your computer. Remember to set the 5V_SEL jumper

to VUSB so that the board gets powered through USB. If your computer does not detect the board, you may need to install drivers to support CH340 on your operating system. - Windows: http://www.wch.cn/download/CH341SER_EXE.html - Mac: http://www.wch.cn/downloads/CH341SER_MAC_ZIP.html - Linux (should already come with the OS):

http://www.wch.cn/downloads/CH341SER_LINUX_ZIP.html - If using Marlin, refer to the instructions at http://marlinfw.org/docs/basics/install.html

for the basics on configuring, building, and uploading Marlin firmware. Here, we will use Arduino IDE to build and upload the firmware. (Note: It is highly recommended to compile Marlin firmware using PlatformIO on VSCode. The specific instructions can be found here http://marlinfw.org/docs/basics/install_platformio_vscode.html.) - First, you need Arduino IDE installed on your computer (Windows, Mac, or

Linux). Go to Arduino IDE's download page (https://www.arduino.cc/en/main/software) to download the version of the IDE for your computer. Arduino IDE's installation guide can be found here. (https://www.arduino.cc/en/Guide/HomePage) - Once Arduino IDE has been installed, follow the instructions here to install the

ESP32 core for Arduino IDE. It is recommended to install the stable release. - Launch Arduino IDE, and open the sketch for the firmware. This file is named

Marlin.ino and can be found in the downloaded firmware's Marlin subdirectory. - In the IDE's menu, go to “Tools”, then “Board”, and choose “ESP32 Dev

Module” which is the generic ESP32 module. Then, under “Tools”, “Port”, choose the COM port that your board is connected to. For upload speed, go to

“Tools”, “Upload speed”, and set to “115200”. - Edit the Configuration.h and Configuration_adv.h files to define

the size of your printer, endstops, and other settings. See the section below for some basic settings which need to be changed. - Click on the “Upload” icon of the IDE to compile the firmware and flash it onto the board. This will take quite a while. - Once the firmware has been flashed onto the board, you can open the IDE's

serial monitor (by pressing Ctrl+Shift+M, or from the menu via Tools, then Serial monitor) to make sure the firmware has been flashed properly. Enter M503 into the serial monitor and you should get a response from the board giving the current settings such as steps/mm and PID values. - Via the serial monitor, you can configure your WiFi settings. See the section

below on how to do so. You can also set up WiFi using a web browser (see relevant section below). - When uploading firmware for the first time, the board needs to be connected via USB

to the computer. Once over-the-air (OTA) update has been enabled, future uploads of firmware to the board can be carried out via WiFi. Setting up WiFi (via Terminal)

Once the firmware has been flashed for the first time, there is a need to do an initial setup for the WiFi settings. In Arduino IDE, open up the serial monitor to connect to the board. You can also use any other terminal program to open the COM port that the board is connected to. Then, type in the following commands 1, 2, and 5 to set up the board in station mode

(connect to an existing WiFi router). To set up in AP mode, use commands 3, 4, and 5. 1. [ESP100]abcd

## [ESP101]12345

WiFi settings; the above will connect to a SSID of abcd with password 12345. Change abcd and 12345. 2. [ESP103]STA

This will start up WiFi in station mode. The IP address of the webserver will be displayed in the terminal. Use this IP address to connect to the webserver. 3. [ESP105]abcd

## [ESP106]12345

WiFi settings; the above will create an access point with SSID of ESP32 and password 12345. WPA2 security will be used by default. 4. [ESP103]AP

This will start up WiFi in AP mode. 5. [ESP110]ON

This will turn on WiFi. Setting up WiFi (via WiFi)

When WiFi is not configured, the board will automatically become an access point (AP). The SSID of this AP is MARLIN_ESP and the default password is 12345678. Connect your computer to this AP, then open a web browser and go to the address 192.168.0.1 to open up a web interface to configure WiFi settings. For login credentials, use the user name admin and the default password admin to change the settings. Uploading the web UI - When you first go to the web UI address (if you have mDNS, this should be

http://marlinesp.local/ by default), you will be asked to upload the web UI files. Click on "Choose files", select index.html.gz, then upload. Then, refresh your browser page; the webUI should load. A copy of index.html.gz can be found in the firmware directory, under <firmware directory>/Marlin/data/. - If you have the Arduino ESP32 filesystem uploader, you can also choose to upload the

required files from Arduino IDE. After flashing the firmware, go to Tools, then choose ESP32 Sketch Data Upload.

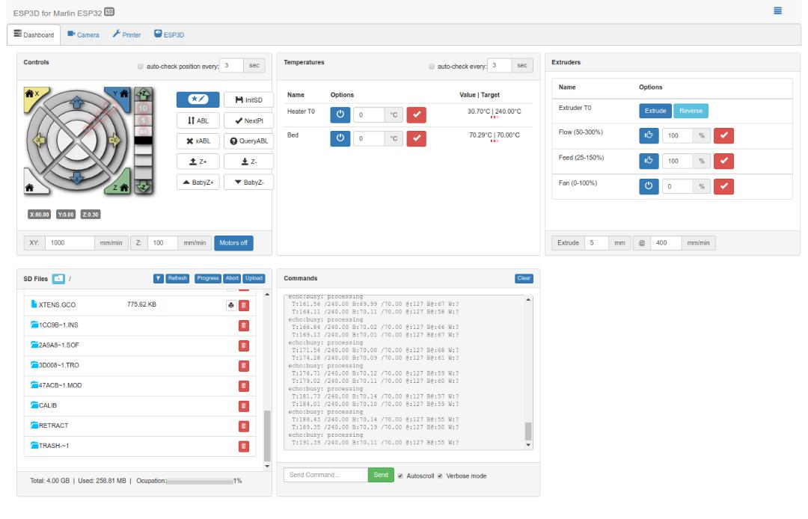
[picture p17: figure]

Adding macros
The webUI (based on ESP3D) allows user-defined macros to be created. This allows “buttons” for custom commands (GCODE), such as buttons for babystepping, to be added to

the webUI. For example, to add a command to move to babystep Z by 0.01 downwards:

1. Create a text file with the gcode. In this case the gcode would be “M290 Z-0.01”.

Save it with a “.g” extension. In this case, it can be named babyzdn.g. 2. Upload that file to the ESP3D File System (not to the SD card); this is the SPIFFS file

system, where index.html.gz is stored. 3. Click on the macro editor button in the controls panel. click the plus icon to add a

macro. Give it a name, select a color, set the target as ESP and enter the path to the gcode file you uploaded. 4. Click Save. Some ready-made macros can be found at:

https://github.com/maplerainresearch/MRR_ESPA/tree/master/firmware/macros

### Additional Notes

Wi-Fi performance
- Avoid placing the MRR ESPA within a metal case as it may adversely affect Wi-Fi performance. If necessary, expose the PCB antenna outside the case. Connecting Trinamic stepper motor drivers (SPI mode) - Jumpers are available to allow Trinamic stepper motor drivers using SPI mode to be

easily configured. By setting the jumpers correctly, the only wiring needed for each driver is a wire for the CS pin. - To configure a driver for SPI mode, connect the jumpers MS1, MS2, MS3, and RST

for that respective driver to the TMC side.

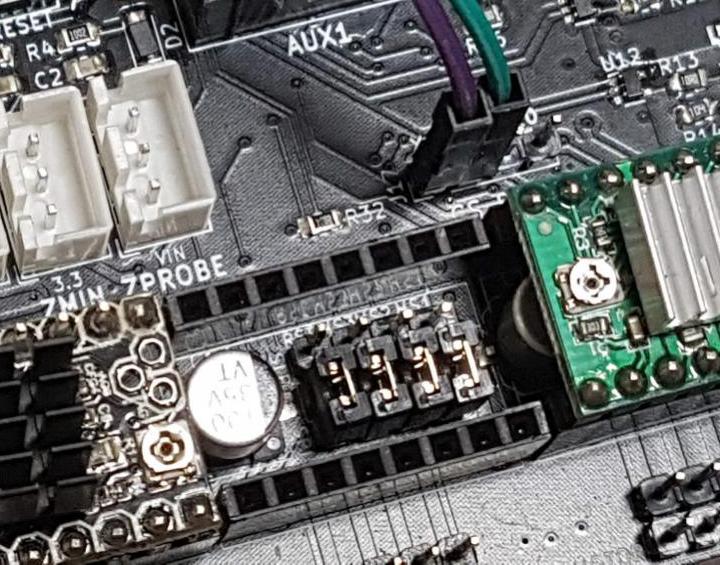
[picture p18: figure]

- Use a jumper wire to connect the respective CS_PIN (either X, Y, Z, or E0) to an unused pin (IO0, SDA, or SCL).

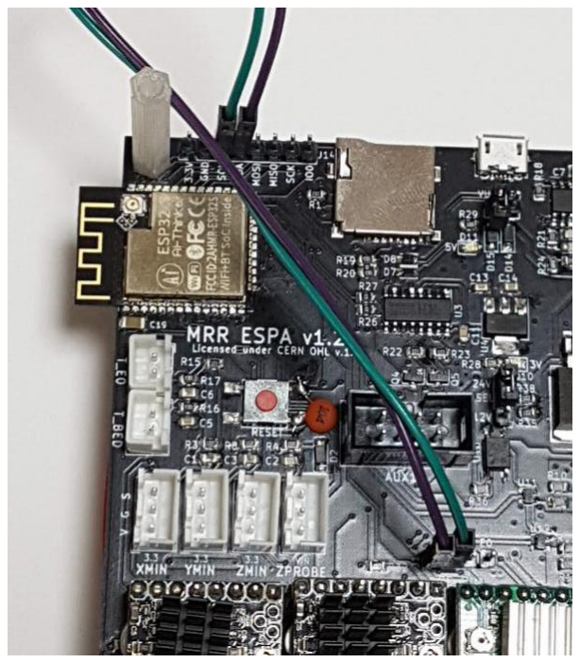
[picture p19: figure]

Using 12V for heated bed
- When using 12V for the heated bed, the current drawn by the heated bed can be in excess of 10A. This can cause the board to become very hot; do not touch the board during operation. (Warning: Parts of the board, such as the VBED fuse, can reach temperatures above 100 degrees Celsius when heating the heated bed. Also, due to the high currents involved, wires use for the heated bed, including wires being used to connect to the PSU, may get very hot.) - It is highly recommended to have another fan to cool the underside of the board. This

fan can be connected in parallel with the case fan. It is also recommended to place a small heat sink on the heated bed MOSFET (Q1). Using GPIO0 (IO0)

On the ESP32, GPIO0 has a special function: it is pulled to GND when booting to enter flash mode. Therefore, it is not recommended to use this pin for functions which require it to be physically pulled to GND, as it will affect the booting up of the board. On the other hand, if you are facing problems trying to flash the board via USB, you can

connect GPIO0 to GND, then reset the board to enter flash mode.

### Troubleshooting

A common cause of issues with the board is a loose connection. Check to make sure all cables are firmly connected. Reverse polarity can also damage the board, so check that all cables are connected with correct polarity. - Issue: The endstops are not triggering. Check the endstops are connected correctly, especially the V, G, and S wires. Mechanical endstops usually only require two wires: ground (connect to G) and the

signal line (connect to S). - Issue: The motors do not move. Make sure the jumpers under the stepper drivers are connected correctly. For A4988

or DRV8825 drivers, the RST jumper must be connected to the SLP side. The other jumpers (MS1, MS2, MS3) can be connected to VIO to pull them high (to set microstepping), or left unconnected. - Issue: The heated bed does not heat up. The heated bed is powered via VBED, so make sure there is a power supply

connected to VBED. - Issue: The motors keep stopping during the print. Make sure the stepper drivers are adequately cooled. A case fan should be used to cool

the stepper drivers; this fan is connected to CASE_FAN. - Issue: The motor is turning the wrong way. You can either reverse the cable connection on the board, or edit the firmware’s

configuration to reverse the direction of the motor. - Issue: Files uploaded to the microSD card using the webUI are corrupted or partially

truncated. Disable #define MONITOR_DRIVER_STATUS in Configuration_adv.h by

commenting it out (adding double backslashes in front of it).

### Warnings

- This product uses high currents which may cause fires. Use with caution. - Do not use input voltages higher than 24V. Input current must not exceed 15A. - Do not attempt to use more than 15A for the heated bed. While the MOSFET is

capable of such currents, the connectors are not. If you need more than 15A, use an external MOSFET. In any case, it is highly recommended to use an external MOSFET for the heated bed to avoid drawing high currents through this product. - Do not attempt to use more than 5A for the hot end. While the MOSFET is capable of

such currents, the connectors are not. If you need more than 5A, use an external MOSFET. - Do not reverse polarity. - The breakout and endstop pins are rated for 3.3V, which is the voltage the ESP32

operates at. Attempting to feed inputs above 3.3V to these pins may damage the board. - It is recommended to power the board only via USB (i.e. turn off PSU power supply)

when flashing the board. Disclaimer

This product is provided as-is. While care has been taken to design a safe product, it is the user's responsibility to make sure precautions are taken to prevent damage or injury when using this product. This includes adhering to all warnings provided. By using this product, the user accepts responsibility to bear all liabilities from any damage or injury arising from the use of this product. License

Released under CERN Open Hardware Licence v1.2.

### Additional Information

Common Marlin settings
Below are some common settings in Marlin firmware which should be set to reflect your machine setup. This is not a comprehensive nor exhaustive list; the user is recommended to

## go through each setting in Configuration.h and Configuration_adv.h to make

sure all settings are correct. Note: Enabling a feature/setting means to uncomment it, i.e. make sure there is no // (double

slashes) in front of the #define statement. Configuration.h

#define MOTHERBOARD

This value defines which board is being used. It should be set to #define MOTHERBOARD BOARD_MRR_ESPA for the MRR ESPA. #define BAUDRATE

This is the speed used for serial communications. It should be set to #define BAUDRATE 115200 for the MRR ESPA. #define TEMP_HYSTERESIS

#define TEMP_BED_HYSTERESIS

These values define what is considered “close enough” when trying to reach a certain temperature for the hotend or heated bed. Due to the ADC of the ESP32, they should be set to a value of 5. #define PIDTEMPBED

This allows PID bed heating, and should be enabled. #define THERMAL_PROTECTION_HOTENDS

#define THERMAL_PROTECTION_BED

#define THERMAL_PROTECTION_CHAMBER

These settings enable safeguards against a broken or disconnected thermistor wire, and must be enabled. #define X_DRIVER_TYPE

#define Y_DRIVER_TYPE

#define Z_DRIVER_TYPE

#define E0_DRIVER_TYPE

Change the values of these to reflect the stepper driver being used for each axis. The default value is A4988. #define INVERT_X_DIR

#define INVERT_Y_DIR

#define INVERT_Z_DIR

#define INVERT_E0_DIR

Toggle these values between true and false to switch the direction of the stepper motors. #define X_HOME_DIR

#define Y_HOME_DIR

#define Z_HOME_DIR

The values of these should be -1 to use the minimum endstops. #define X_BED_SIZE

#define Y_BED_SIZE

#define Z_MAX_POS

These values should be set to the maximum sizes for your X, Y, and Z axes respectively. #define X_MIN_POS

#define Y_MIN_POS

These values reflect the position of the nozzle when the respective X and Y minimum endstops are triggered. Set to values of 0 if the endstops are triggered at the edges of the print area. Set to negative values if the endstops are triggered with the nozzle outside the print area. #define Z_MIN_POS

This value reflects the position of the nozzle when the Z minimum endstop is triggered. Set to 0 if the endstop are triggered at same height as the bed, or if using an autolevel probe. Set to a negative values if the endstop is triggered with the nozzle below the bed. #define Z_SAFE_HOMING

Enable this if you are using an autolevel probe and want to home the Z axis using the center of the bed instead of at the edge (where the probe may fail to detect the bed). #define SDSUPPORT

This must be enabled to allow use of the onboard microSD card. #define SPI_SPEED SPI_HALF_SPEED

Enable this if you have “volume init” errors. Configuration_adv.h

#define TX_BUFFER_SIZE

Set to 128 for optimal speed. #define RX_BUFFER_SIZE

Set this to at least 1024. #define X_CS_PIN -1

#define Y_CS_PIN -1

#define Z_CS_PIN -1

#define E0_CS_PIN -1

If using Trinamic stepper drivers in SPI mode, uncomment the respective line for the axis, and change the -1 to the pin being used for CS (such as 21 or 22). #define ESP3D_WIFISUPPORT

#define WEBSUPPORT

#define OTASUPPORT

#define WIFI_CUSTOM_COMMAND

Enable this to allow the MRR ESPA to communicate via WiFi using the ESP3D webUI, and allow over-the-air (OTA) updates. Pins
Function | Marlin name | Pin
| Endstops
X min endstop | X_MIN_PIN | 34
Y min endstop | Y_MIN_PIN | 35
Z min endstop | Z_MIN_PIN | 15
Stepper drivers
X step | X_STEP_PIN | 27
X direction | X_DIR_PIN | 26
X motor enable | X_ENABLE_PIN | 25
Y step | Y_STEP_PIN | 33
Y direction | Y_DIR_PIN | 32
Y motor enable | Y_ENABLE_PIN | X_ENABLE_PIN
Z step | Z_STEP_PIN | 14

Z direction | Z_DIR_PIN | 12
Z motor enable | Z_ENABLE_PIN | X_ENABLE_PIN
E0 step | E0_STEP_PIN | 16
E0 direction | E0_DIR_PIN | 17
E0 motor enable | E0_ENABLE_PIN | X_ENABLE_PIN
Thermistors
Hotend thermistor | TEMP_0_PIN | 36
Heated bed thermistor | TEMP_BED_PIN | 39
Heating elements
Hotend MOSFET gate | HEATER_0_PIN | 2
Heated bed MOSFET gate | HEATER_BED_PIN | 4
Fan
Part cooling fan | FAN_PIN | 13
| MicroSD card
SD card select | SDSS (or SS_PIN) | 5
| SPI pins
MOSI | MOSI_PIN | 23
MISO | MISO_PIN | 19
SCK | SCK_PIN | 18
I2C pins
SDA | SDA (not used) | 21
SCL | SCL (not used) | 22
Others
GPIO0 | (not used) | 0

Document Revision History
October 24, 2019
- Document created. January 14, 2020
- Updated with new ESP3D commands and configuration requirements due to ESP3DLib integration into Marlin. - Added note about issue with MONITOR_DRIVER_STATUS causing problems with

SD file uploads.

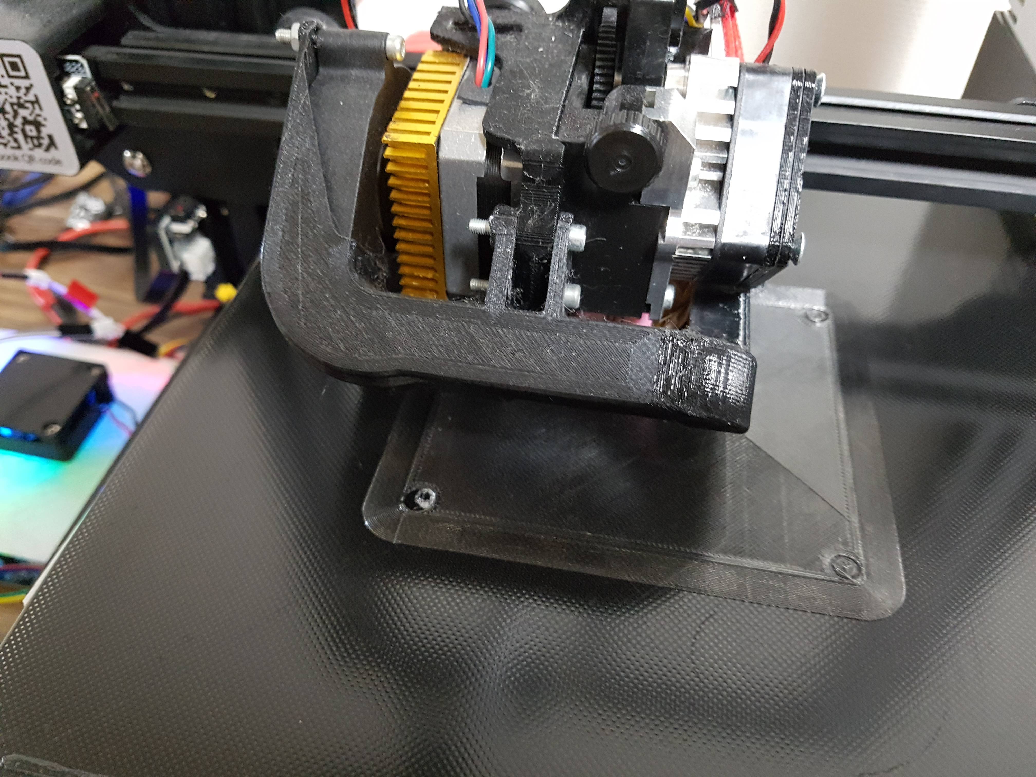
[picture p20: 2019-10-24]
media/test printing clear pla.jpg

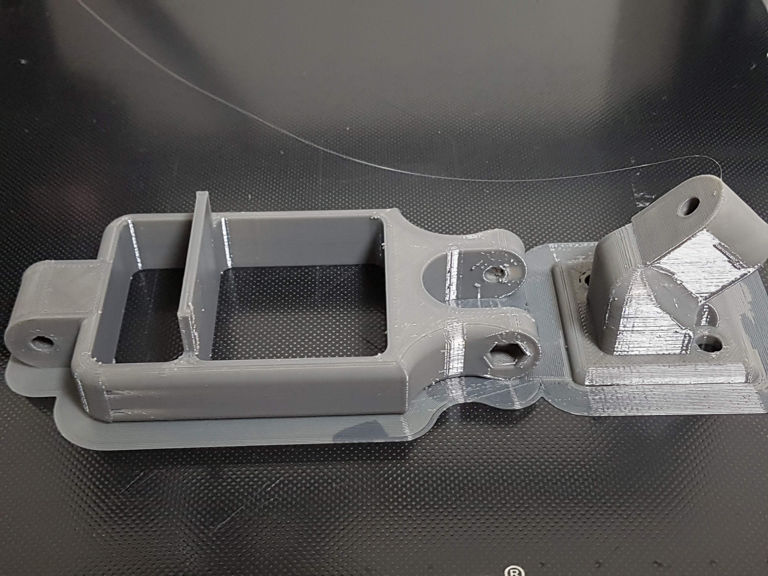
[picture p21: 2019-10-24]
media/test print petg 1.jpg

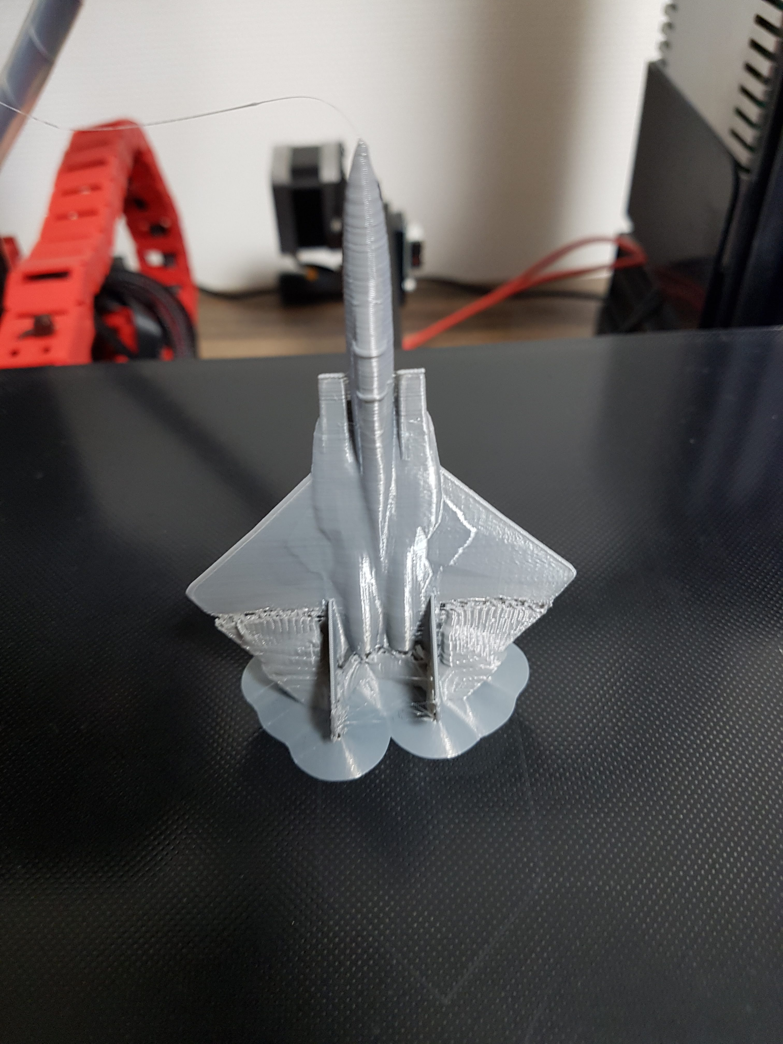
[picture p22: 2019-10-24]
media/test print completed.jpg

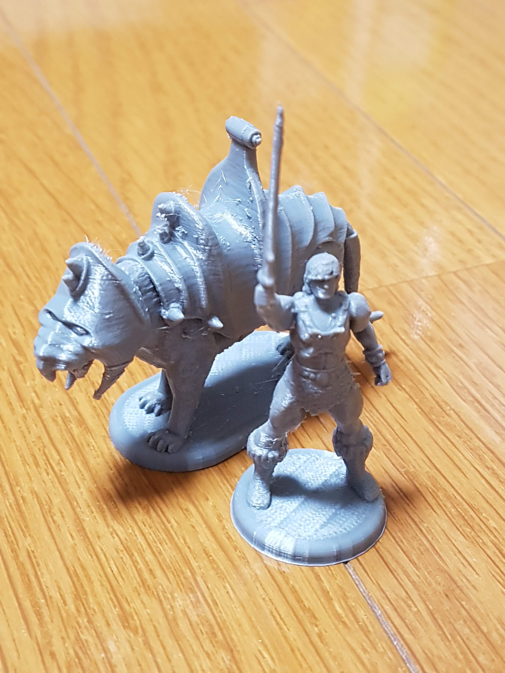
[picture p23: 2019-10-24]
media/test print pla 2.jpg

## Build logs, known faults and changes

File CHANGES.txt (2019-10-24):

Changes
-------
v1.3
----
- Added debounce capacitor to RESET button.
- Change VUSB_EN jumper to 5V_SEL jumper, to select between VUSB and VIN for 5V source.
- Changed F1 to 15A (Littelfuse 0451), F2 to 30A (Littelfuse 0456).

v1.2
----
- Changed MOSFETs to Winsok MOSFETs (bed: WSK220N04; E0: WSF3085; fan: WSF3038).
- Added jumper to disable VUSB.
- Added PWR_SEL jumper to choose if voltage divider should be used for gate voltage of bed MOSFET (use voltage divider for 24V, skip voltage divider for 12V).
- Added TMC2130 jumpers. Switch jumpers under stepper drivers to SPI side, then use jumper wires to connect the desired CS pins to an unused pin (0 [IO0], 21 [SDA], or 22 [SCL]).
- Change layout of TPS54340-related circuit to follow recommended PCB layout in data sheet.
- See v1.1 for other production-related changes.

v1.1
----
- Production version.
- Removed header pins for those pins already used.
- UART header removed as it is redundant with AUX1.
- Level shift resistors for AUX1 removed as ESP32 is 5V tolerant when powered with 3.3V.
- Endstop and thermistor connectors changed to JST XH connectors. Stepper motor connectors continue to use generic 2.54mm pitch male headers so as to be easy to flip around.
- Board size reduced to 99.5mm by 90.5mm.
- Unused pins are IO0, IO21 (SDA), and IO22 (SCL).

v1.01
-----
- Widened VBED-related trace widths to solve issues with high temperatures when heating. 

v1.0
----
- Widened trace width of high current bearing lines, like those used for the heatbed and hotend. Changed via diameter for VBED line to match the track width; the diameter used in previous versions was too small, causing excessive heat buildup and burning the PCB.
- Exposed underside of PCB for MOSFETs and VBED terminals for better heat dissipation.
- Removed TXS0102 level shifter; used a simple voltage divider on RX pin, while TX pin is left as it is.
- Amended jumpers for stepper drivers; changed to connect to either VIO, GND, or unconnected. Removed CS_PIN headers, unrouted SPI nets (MOSI, MISO, SCK) from stepper drivers. TMC2130 drivers can be connected in standalone (non-SPI) mode by removing all the jumpers under the driver. For TMC2208 drivers, MS1 and MS2 can be connected to GND or VIO to set microstepping in standalone mode; remove MS3 and RST jumpers. TMC2130 drivers with their SPI pins exposed on top can be connected to the board's SPI pins (for CS, use one of the unused ESP32 pins such as SDA, SCL, or IO0).

v0.9
----
- TLP182 (SMD-4) optocoupler and voltage divider to drive bed MOSFET so that a separate PSU can be used, referencing Little-Driver (https://github.com/Digital-Sqrt/Little-Driver).
- 74LVC1G125 (SOT-353) to drive E0 and fan MOSFETs.
- TXS0102 level shifter for AUX1; allows AUX1 to be used with 5V logic. The TXS0102 will translate the UART (RX and TX) bidirectionally between 5V (AUX1) and 3.3V (ESP32).
- Remove 5V select circuit; switched to using 1N5819 diodes to prevent reverse voltage.
- Amended several capacitors which were mistakenly connected in series instead of in parallel. Specifically, C11 and C12 in v0.8.
- Amended DTR/RTS circuit; previously, IO0 connected to wrong side of S9014, which prevented flashing of firmware via USB.
- Fixed microSD card connections (MISO and MOSI were connected in reverse).

v0.8
----
- Renamed as MRR ESPA.
- Migrated to KiCad.
- Shifted position of ESP32 to expose the antenna outside the board. Also, reduced the routing of lines under the ESP32 module to prevent interference.
- Removed 74HCT125; the MOSFETs used can perform adequately well at 3.3V logic without having to translate up to 5V. The footprint freed up will be used to house 74HC595s in version 2 of the board to utilize I2S for motor control.
- Instead of 74HCT125, BSS138 transistors have been added for level translation to drive MOSFETs at 5V.
- Removed Vout_SEL jumper. Breakout pins will be 3.3V; 5V can be obtained from AUX1.
- Changed F2 fuse to 10A fuse. Previously 3A, not enough to support hotend.
- Added decoupling capacitor for ESP32.
- TX/RX lines have been routed as far as possible as a differential pair.
- EN button renamed "RESET" on the board.

v0.7
----
- Added capacitors to endstops for filtering.
- Changed thermistor resistors to 4.7K (original 47K was mistake).
- Removed TMC2208 PD_UART jumpers as the current setup does not have enough sets of TX/RX pins to support at least 2 drivers (X and Y).
- Removed button for IO0.
- Renamed "EN" button to "BOOT" button.
- Added capacitors to 3.3V regulator for more stable power.
- Replaced 5V step-down circuit. Uses TPS54340 instead of LM2596 for a smaller footprint. Circuit was designed using TI's Webench. Previous LM2596 circuit was using an underspec inductor (540mA) instead of something over 4.5A. Space freed up will eventually be used in version 2 of the board, which will incorporate I2S.
- Replaced 74HCT02 with 74HCT125, which is a non-inverting buffer gate. May eventually be switched to I2S in version 2 if I2S can stably run MOSFETs.
- Added MOSFET enable jumper (MOS_EN). When testing the rest of the board, this jumper can be left open to disable the 74HCT126.
- Replaced 5V_SEL jumper with an OPAMP and P-channel MOSFET instead, to avoid power problems should the user forget to set the jumper correctly. This selection circuit is similar to that being used on the Arduino UNO R3.

v0.6
----
- Changed capacitors for motor drivers to 100uF.
- Changed bed mosfet to IRLS3034PBF, which has a lower on-resistance at 4.5V.
- Used 74HCT02 to drive mosfets.

v0.5
----
- Added jumpers to allow TMC drivers to be used.
  - Connect or disconnect MS1, MS2, MS3 jumpers for normal microstepping control (A4988, etc.).
  - Connect RST to SLP for normal drivers like A4988.
  - Connect MS1, MS2, MS3, RST jumpers to TMC side for TMC2130.
  - Connect RST jumper to TMC side for TMC2208; MS1 and MS2 can still be used for microstepping.
  - Connect TMC_SEL jumper to SPI for TMC2130, and UART for TMC2208.
  - When using TMC2130 SPI, connect X, Y, Z, or E0 pin on CS_PIN row to the pin that is to be used for CS on the ESP32 breakout row.
- Fixed missing nets on v0.4 PCB.

v0.4
----
- Renamed power inputs to VIN and VBED.
- Changed reverse current protection diodes to parallel instead of series.

v0.3
----
- Initial release on Github.
- Changed to use 5.08mm pitch terminals instead of 7.62mm pitch terminals to reduce footprint.
- Added AUX1 connector.

v0.2
----
- Overhaul of v0.1 to use ESP32-WROOM-32 module instead of development boards.
- Added design consideration to fit within 100mm x 100mm of PCB area.
- Support for 4 stepper drivers, single hot end, single heat bed, single part cooling fan.
- Pinout based on current (2018-11-25) pins_ESP32.h of Marlin firmware (bugsfix-2.0.x branch).

v0.1
----
- Based on 2 x LOLIN32 development boards, with one running Marlin firmware, and another running ESP3D to provide user interface.

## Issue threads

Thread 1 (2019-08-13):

Feedback on MRR ESPA

vivian-ng, 2019-08-13:
TMC2130 support for Marlin 2.0 bugsfix has been successfully compiled to run with ESP32. A native ESP32 pin needs to be used for the CS pin, for example, GPIO21 (SDA) or GPIO22 (SCL).

TMC2208 and TMC2209 drivers will need a bit more work, since they will likely need to use software serial, and there are currently issues with compiling software serial on TMCStepper library:
[ESP32 is no SoftwareSerial Compatible Platform](https://github.com/teemuatlut/TMCStepper/issues/59)
[ESP32 compatibility](https://github.com/teemuatlut/TMCStepper/issues/35)
Each of these drivers also needs 2 native ESP32 pins, which is a luxury that cannot be easily spared since the ESP32 has very few pins to start with in the first place. So it is unlikely the board will ever be designed to support TMC2208/TMC2209 drivers via jumper settings, because at most, it will only be able to support ONE single axis given the number of spare pins available.

For SPI mode, users will just need one jumper wire (female-to-female) per stepper driver to connect the CS pin for the respective axis to a spare pin (GPIO0, GPIO21, and GPIO22).

vivian-ng, 2019-09-17:
I have finally managed to find a PCB manufacturer to get a proper quote. I have launched this project on Kickstarter based on the quote to make it available to everyone who wants one but do not have the time/resources to make one themselves. The reward is priced at cost: 76.5% production and shipping, 5% Kickstarter fees, 4.5% Kickstarter payment provider fees, 6% bank fees, 8% taxes.

For those who already have the required components on hand, making your own board by ordering a PCB (from JLCPCB, for example) is the cheaper option. But for those with no such components, I think backing this Kickstarter is the easy (and cheaper) way since the unit price is based on a larger production volume.

Anyway, here is the link:
[MRR ESPA Kickstarter page](https://www.kickstarter.com/projects/maplerainresearch/mrr-espa)

h55ia, 2019-09-17:
No UART, then it's not for me, hope another version releases with UART in the future, but nonetheless thank you for doing this

vivian-ng, 2019-09-17:
@h55ia No problem! Thanks for being interested.

Anyway, it is unlikely that any ESP32 board I came up with in the future will support TMC drivers in UART mode. SPI, yes. UART, no. Because the ESP32 only has 3 sets of hardware serial, and one of those is already being used by the serial terminal (CH340). Which leaves only two, for probably X and Y axis at best. Even if more pins are available, software serial for the ESP32 now is still... not really ready to support this. Also, TMCStepper library (used by Marlin for TMC drivers) currently does not support software serial for ESP32, and unless someone takes the time to work on that, is unlikely to in the near future.

If UART is a gamebreaker for you, one possibility is to get any of the new STM32-based boards tested working with TMC2208 or TMC2209 in UART mode. Then, connect a ESP32 with ESP3D flashed on it to the STM32-based board via serial. WiFi and ESP3D won't be native on that STM32-based board, but at least it will have WiFi and a web interface. And UART.

vivian-ng, 2019-10-09:
1. Update on thermals. I think I managed to find the issue with my thermal problems. The reason why the fuse is getting so hot during the heating of the heated bed is because my heated bed is not 180W (@12V) as I thought it was supposed to be. I measured the current when heating, and it was registering 24A! Obviously, that is not good news for my fuse, which is rated for 20A. No wonder my fuses were getting hot, and after sustained heating, breaking (as they are supposed to). But at least the terminals held out, and did not burn.
The VBED fuse will be changed to 30A ones.

2. Update on Kickstarter. This update is a bit late since the project funding period has been over for more than a week, but the funding goal was not met, so for the moment, "mass" production will not be taking place. Still, I will see if I can get a few pieces put together and sell it directly to those who want one.

luc-github, 2019-10-12:
@vivian-ng do you have a youtube video showing your board features  in action ? This would complete the one you have on kickstarter which show pictures but no live action.
This would help to communicate on your boards I thinlk

vivian-ng, 2019-10-12:
@luc-github I do have some other videos, including the Kickstarter video, on YouTube.

[Kickstarter video](https://www.youtube.com/watch?v=s4IRmG6ibc4)
[Using a smartphone to control a 3D printer](https://www.youtube.com/watch?v=VrA9YzNtQDA)
[Another webUI video](https://www.youtube.com/watch?v=E-ERUolL-Bw)

Anyway, I will hand solder a few boards, and set up a page for people who are interested to directly buy using PayPal payment. Have to find time to set up that page, though.

luc-github, 2019-10-12:
weird. When I type Marlin ESP32 in youtube search none of them pop up . May be they need some keyword

vivian-ng, 2019-10-26:
# Please use the new [repo](https://github.com/maplerainresearch/MRR_ESPA) for further discussions about the MRR ESPA.
All the latest files are on the new [repo](https://github.com/maplerainresearch/MRR_ESPA). I will keep this issue open so that it serves as a reference for those who are interested to know the development background.
# Any new issue should be posted on the new [repo](https://github.com/maplerainresearch/MRR_ESPA).

luc-github, 2019-10-27:
@vivian-ng you need to enable `issues`  in your repository settings ^_^

vivian-ng, 2019-10-28:
@luc-github Thank you for the tip!
BTW, can you email me your address at info_at_maplerain.com?
I want to send you the MRR ESPA and MRR ESPE (current versions).

vivian-ng, 2019-11-13:
I have made the MRR ESPA v1.3 available [here](https://www.maplerain.com/en/products/mrr-espa-prelaunch) for those who wish to try one without having to get all the parts and solder everything by yourself. I have been using this version for quite a while now and it has been running quite smoothly.

If you have a smart phone or tablet lying around, you can even use it as a on-demand controller. That's what I do because my printer is located a distance away from my PC. While I usually control my printer via the PC, I have an unused smart phone near the printer so that I can control the printer from nearby too (such as when doing manual mesh bed leveling or loading filament).

vivian-ng, 2019-12-12:
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

This is the reason why SDA and SCL are purposely left unused on the MRR ESPA. I knew that ESP3D supported OLED displays via I2C, and also knew that the ESP32 did not have enough pins to support a LCD controller like the RepRap full graphics smart controller. So the MRR ESPA was designed to have the I2C pins (SDA and SCL) unused so that they can eventually be used to connect some kind of controller over I2C.

Now, the OLED display has been tested to work. The only thing remaining is to find some form of I2C rotary encoder (like this one [here](https://hackaday.com/2018/04/15/rotary-encoders-become-i2c-devices/)) and get it to work in Marlin.

To enable OLED display, uncomment
`#define U8GLIB_SSD1306`
in `Configuration.h`.

vivian-ng, 2020-01-16:
See this [comment](https://github.com/maplerainresearch/MRR_ESPE/issues/1#issuecomment-573967923) about MONITOR_DRIVER_STATUS conflicting with SDSUPPORT when using TMC drivers in SPI mode.
See this [comment](https://github.com/maplerainresearch/MRR_ESPE/issues/1#issuecomment-574941070) for the PR.

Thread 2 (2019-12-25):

MRR ESPA with Trinamic drivers in UART mode

vivian-ng, 2019-12-25:
I received an email asking about TMC2209 drivers in UART mode. I thought it best to move the conversation to a more public space so that the collective wisdom of the open source community can be harnessed.

First, @luc-github has managed to use TMC2208 in standalone (aka "dumb") mode which does not use UART at all. Basically, the driver is configured using jumper pins much like normal "dumb" drivers like A4988.

For the MRR ESPA, the issues with getting UART mode working are:
1. **Lack of pins**. Currently, there are only 3 free pins on the board. There are other pins that can be freed (bed heating pin, if a heated bed is not used; MOTOR_EN_PIN, if the motors are always enabled) but that gives at the very very most 5 pins. Each axis requires 2 pins for UART, which means at most, this board can support only 2 axes on TMC drivers in UART mode.
2. **Hardware serial**. While the ESP32 has 3 sets of hardware serial, I have seen a lot of articles regarding getting all 3 to work. Most can get 2 sets working. One set will be used for serial terminal (USB to UART) already; that leaves only one other set of hardware serial for TMC driver in UART mode.
3. **Software serial**. The lack of hardware serial is usually overcome with software serial. But software serial support for ESP32 on the TMCStepper library is still being worked on. Unless someone is able to work on the software development for this, software serial will not be an option at all. Remember, even if software serial support is somehow developed, there is still the issue with a lack of pins.

Consolidating:
- Trinamic drivers in standalone mode works.
- Trinamic drivers in SPI mode works. If you need silent operations, TMC2130 drivers can be used. For higher currents, TMC5160 should work too.
- Trinamic drivers (TMC2208 and TMC2209) in UART mode has the limitations as outlined above.

vivian-ng, 2019-12-25:
For use of Trinamic drivers in UART mode on the MRR ESPE (which uses I2S for stepper and PWM), see this [issue](https://github.com/maplerainresearch/MRR_ESPE/issues/2).

Please feel free to join in the conversation.

vivian-ng, 2020-01-29:
I was not very informed about the TMC2209 stepper drivers. TMC2208 has a fixed slave address, which is 0, and that means only one driver can be on the same UART port since there isn't any addressing capability. But TMC2209 allows configuration of up to four different slave addresses (0 to 3). This means up to four stepper drivers can actually share the same UART port. With @luc-github's help, I managed to get two TMC2209 drivers working on the same hardware serial on the MRR ESPA.

See this video for a quick look at how to set this up.
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

See this [blog post](https://teck78.blogspot.com/2020/01/setting-up-tmc2209-in-uart-mode-on-mrr.html) for more details.

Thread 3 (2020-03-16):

TODO List

vivian-ng, 2020-03-16:
This is a list of TODO items for the MRR ESPA.

- Redo TMC CS pin header to allow for easy TMC SPI and UART configuration
- Add additional pins for 5V, 3.3V, and VIN
- Add pin for EN
- Add test points for pins which are not broken out

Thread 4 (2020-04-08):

Addressable RGB LED aka NeoPixel

vivian-ng, 2020-04-08:
The MRR ESPA has been tested with NeoPixels. See this [blog post](https://teck78.blogspot.com/2020/04/marlin-esp32-and-rgb-leds.html) for more details.

One issue is that the ESP32 runs on RTOS, and the Adafruit_NeoPixel library used by Marlin results in timing issues.
[ESP32: timing error every 1ms corrupts LED pixel data](https://github.com/adafruit/Adafruit_NeoPixel/issues/139)
[ESP32 Feather Causing Specific Neopixels to get Stuck](https://forums.adafruit.com/viewtopic.php?f=24&t=137339)

There are libraries out there that seem to solve this issue, such as the [WS2812FX](https://github.com/kitesurfer1404/WS2812FX) library. Getting NeoPixels to work with the MRR ESPx boards may entail rewriting the `features/leds` portion in the Marlin code to use the WS2812FX library, which seems to be close enough to the current Adafruit_NeoPixel library that porting should not be that much of an issue. One possibility is a kind of "wrapper" like the one [mentioned here](https://github.com/Yurik72/ESPHomeController/wiki/WS2812-driver-to-remove-flickering).

Maybe someone will be able to do the "porting" and report back any success. But as it is now, it does kind of work if you have only a few NeoPixels, and are willing to live with the first pixel being green on boot.

vivian-ng, 2020-04-13:
For the time being, I read somewhere (forgot where) that calling `show()` a second time can help. So I modified the `show()` method in `neopixel.h` to:

```
  static inline void show() {
    adaneo1.show();
    adaneo1.show();
    #if PIN_EXISTS(NEOPIXEL2)
      #if MULTIPLE_NEOPIXEL_TYPES
        adaneo2.show();
        adaneo2.show();
      #else
        adaneo1.setPin(NEOPIXEL2_PIN);
        adaneo1.show();
        adaneo1.show();
        adaneo1.setPin(NEOPIXEL_PIN);
      #endif
    #endif
  }
```

It did help a bit. At least on boot up, after the initial test sequence (if it is enabled in `Configuration.h`), there is no residual light that remains on. But there are still times when changing colors resulted in one of the pixel/LED being a different color. Still, it is better than nothing. Not a solution, though.

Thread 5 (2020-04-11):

Stepper driver DIR pin not changing properly

vivian-ng, 2020-04-11:
During testing with A4988 stepper driver + 24BYJ28 12V stepper motor, it seems the DIR pin is not changing direction properly. This resulted in random shifts due to skipped steps or moves in the opposite direction.

This phenomenon was not observed when using A4988 with NEMA17 stepper motors.

If anyone experiences the same issues, please report your setup here.

wuxiaoyi88, 2020-04-20:
When I was in the use of efsa used use A4988 stepper driver + 12 v MODEL 17 hs4401 stepper motor with computer on line before and after the printing is also about irregular running around, I began to think is PCB version without welding is good, then switch to WEBUI for printing test link to print will be better than the computer, and then moving range before and after the origin about 0.5 2 mm deviation, in the same machine in other printers board go up to normal, I tried many methods, just haven't found the problem...

vivian-ng, 2020-04-20:
@wuxiaoyi88 Try using this old version of [Marlin](https://github.com/maplerainresearch/Marlin), it was the fork by luc before he came up with ESP3DLib. I just did a test today and it seemed to work fine.

I suspect the problem is with Marlin, there were some major changes made to the stepper routines (see PR#[16128](https://github.com/MarlinFirmware/Marlin/pull/16128)) and that might be the cause of problems with stepper control on A4988 on 12V. I am not sure if there is any problem with A4988 on 24V. A lot more work will need to be done to narrow down the actual problem in Marlin, because there has been quite a few changes to the stepper control since December 2019, and it will be tedious to determine which change actually cause this problem.

wuxiaoyi88, 2020-04-20:
Which version did you test that worked well? Which version did I use? I want to find a version like yours for printing test.

vivian-ng, 2020-04-20:
@wuxiaoyi88 Please try this version here.
[https://github.com/maplerainresearch/Marlin](https://github.com/maplerainresearch/Marlin)

It is the old fork by @luc-github before he developed ESP3DLib. I kept it as an archive in case there is a need to fallback on something that works. Like in this case.

Note to self: test Marlin 2.0.2 to see if issue is likely caused by changes made in [PR#16128](https://github.com/MarlinFirmware/Marlin/pull/16128)

vivian-ng, 2020-05-03:
This is a video demonstrating how steps are being lost in Marlin 2.0.x on the MRR ESPA (ESP32 without I2S stepper stream).
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

The fork by @luc-github (archived [here](https://github.com/maplerainresearch/Marlin)) works fine. But newer versions of Marlin 2.0.x (including bugfix-2.0.x) seems to cause issues with the steps. As mentioned in a [prior comment](https://github.com/maplerainresearch/MRR_ESPA/issues/5#issuecomment-616545619), I think it has to do with the new stepper routine.

> I suspect the problem is with Marlin, there were some major changes made to the stepper routines (see PR#16128) and that might be the cause of problems with stepper control on A4988 on 12V. I am not sure if there is any problem with A4988 on 24V. A lot more work will need to be done to narrow down the actual problem in Marlin, because there has been quite a few changes to the stepper control since December 2019, and it will be tedious to determine which change actually cause this problem.

The motors also sound different, which is why I think it has to do with the stepper routine.

Also, while watching this [video by Andreas Spiess](https://www.youtube.com/watch?v=CJhWlfkf-5M), it seems the ESP32's frequency for handling interrupts can become unstable beyond 200 kHz. I wonder if this is something that would affect Marlin, and if so, maybe there is a need to tune down `STEPPER_TIMER_RATE` to something lower than 2 MHz (maybe 250 kHz like the I2S stepper stream). Wonder if @simon-jouet or @felixstorm has any ideas?

felixstorm, 2020-05-05:
Sorry, but I don't think I can be of much help here, as I only use the I2S stepper stream and also have not followed up with the latest Marlin builds for the last few weeks/months.

I did try to take a short look at the video by Andreas Spiess though and as far as I understand it, he talks about interrupts _triggered externally_ and uses the Arduino framework functions to deal with them. AFAIR the ArduinoESP32 interrupt handling code is a pretty big mess with lots of code running after the actual hardware interrupt came in and before the corresponding application code gets called in the end. This probably needed to be done in order to make the ESP32 core compatible as much as possible to the way interrupt processing has been defined for the Arduino framework some 10+ years ago.
Marlin in contrast uses timers (also interrupts, but internal) and directly uses ESP-IDF functions to setup and handle them, so I do not think that one can transfer Andreas Spiess' observations 1:1 to timer handling in Marlin.

Zannys, 2020-05-14:
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

I work in a board similar of ESPA but using esp32 devkit, like a ramps+arduino, and i noticed this problem too, i'm using DRV8825. When a try this fork of marlin the problems gone and i my printer works fine.

I dont think the problem is the timer configuration, beacuse looking the timer.h is the same in both versions of marlin.

felixstorm, 2020-05-14:
I do not think that it has anything _directly_ to do with either the (hardware) timers or 12V vs. 24V.

But since the timing of the stepper pulses has been made "more accurate" in the code with [PR 16128](https://github.com/MarlinFirmware/Marlin/pull/16128): Has anybody tried to play around with the stepper timing parameters (e.g. reducing `MAXIMUM_STEPPER_RATE` and increasing `MINIMUM_STEPPER_PULSE` from the defaults)?
If a logic analyzer (or an oscilloscope) would be around, one could even compare the outcome of the pulses with the old firmware against with the current one to get a hint on why the steppers now sound different and might even "see" the lost pulses.

vivian-ng, 2020-05-14:
@felixstorm Thanks for the suggestion. I do agree that it is most likely not a timer or voltage issue. I did try to play around with some of the settings in `Configuration_adv.h`.

Settings and values tried:
MINIMUM_STEPPER_PULSE: 1, 2, 3, 5
MINIMUM_STEPPER_POST_DIR_DELAY: 200, 400, 650
MINIMUM_STEPPER_PRE_DIR_DELAY: 200, 400, 650
SLOWDOWN_DIVISOR: 2, 4, 6
BLOCK_BUFFER_SIZE: 16, 64, 256

Not much improvement.

vivian-ng, 2020-08-07:
@luc-github just told me it could be due to a missing `#define` in `HAL.cpp`. This causes the I2S stepper stream to be initiated even on boards not using the I2S stream, like the MRR ESPA.

So one thing to try is to edit `HAL.cpp` such that the `HAL_init()` function is defined as:
```
void HAL_init(void) {
#if ENABLED(I2S_STEPPER_STREAM)
    i2s_init();
#endif
}
```

This should solve the problem. I am a bit busy with other things at the moment so I will only be able to try this some time late. I just thought I would share it here for those who want to give it a try to see if it solves the problem.

luc-github, 2020-08-07:
it was found by @GerogeFu actually

xenotrax, 2020-08-29:
Great!! Thank you all!
I compared the "luc" step.cpp with the official one  ... until I've seen this post.
You saved me from a big headache!

vivian-ng, 2021-03-22:
Should be fixed. Closing.

Closed 2021-03-22.

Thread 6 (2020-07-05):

Unable to open. Sch file,

3dle, 2020-07-05:

vivian-ng, 2020-08-07:
Please provide more details about the actual issue faced. The schematic was designed using KiCad.

Closed 2020-09-29.

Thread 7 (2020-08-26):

Firmware compatibility

mentaluproar, 2020-08-26:
Would this be compatible with reprapfirmware? I hate how configuring marlin works and smoothie has always argued with me but this looks ideal for something like a lower cost duet board.

vivian-ng, 2020-09-06:
@mentaluproar At present, I do not think reprapfirmware supports this board (or any board based on the ESP32, for that matter).

Closed 2020-09-29.

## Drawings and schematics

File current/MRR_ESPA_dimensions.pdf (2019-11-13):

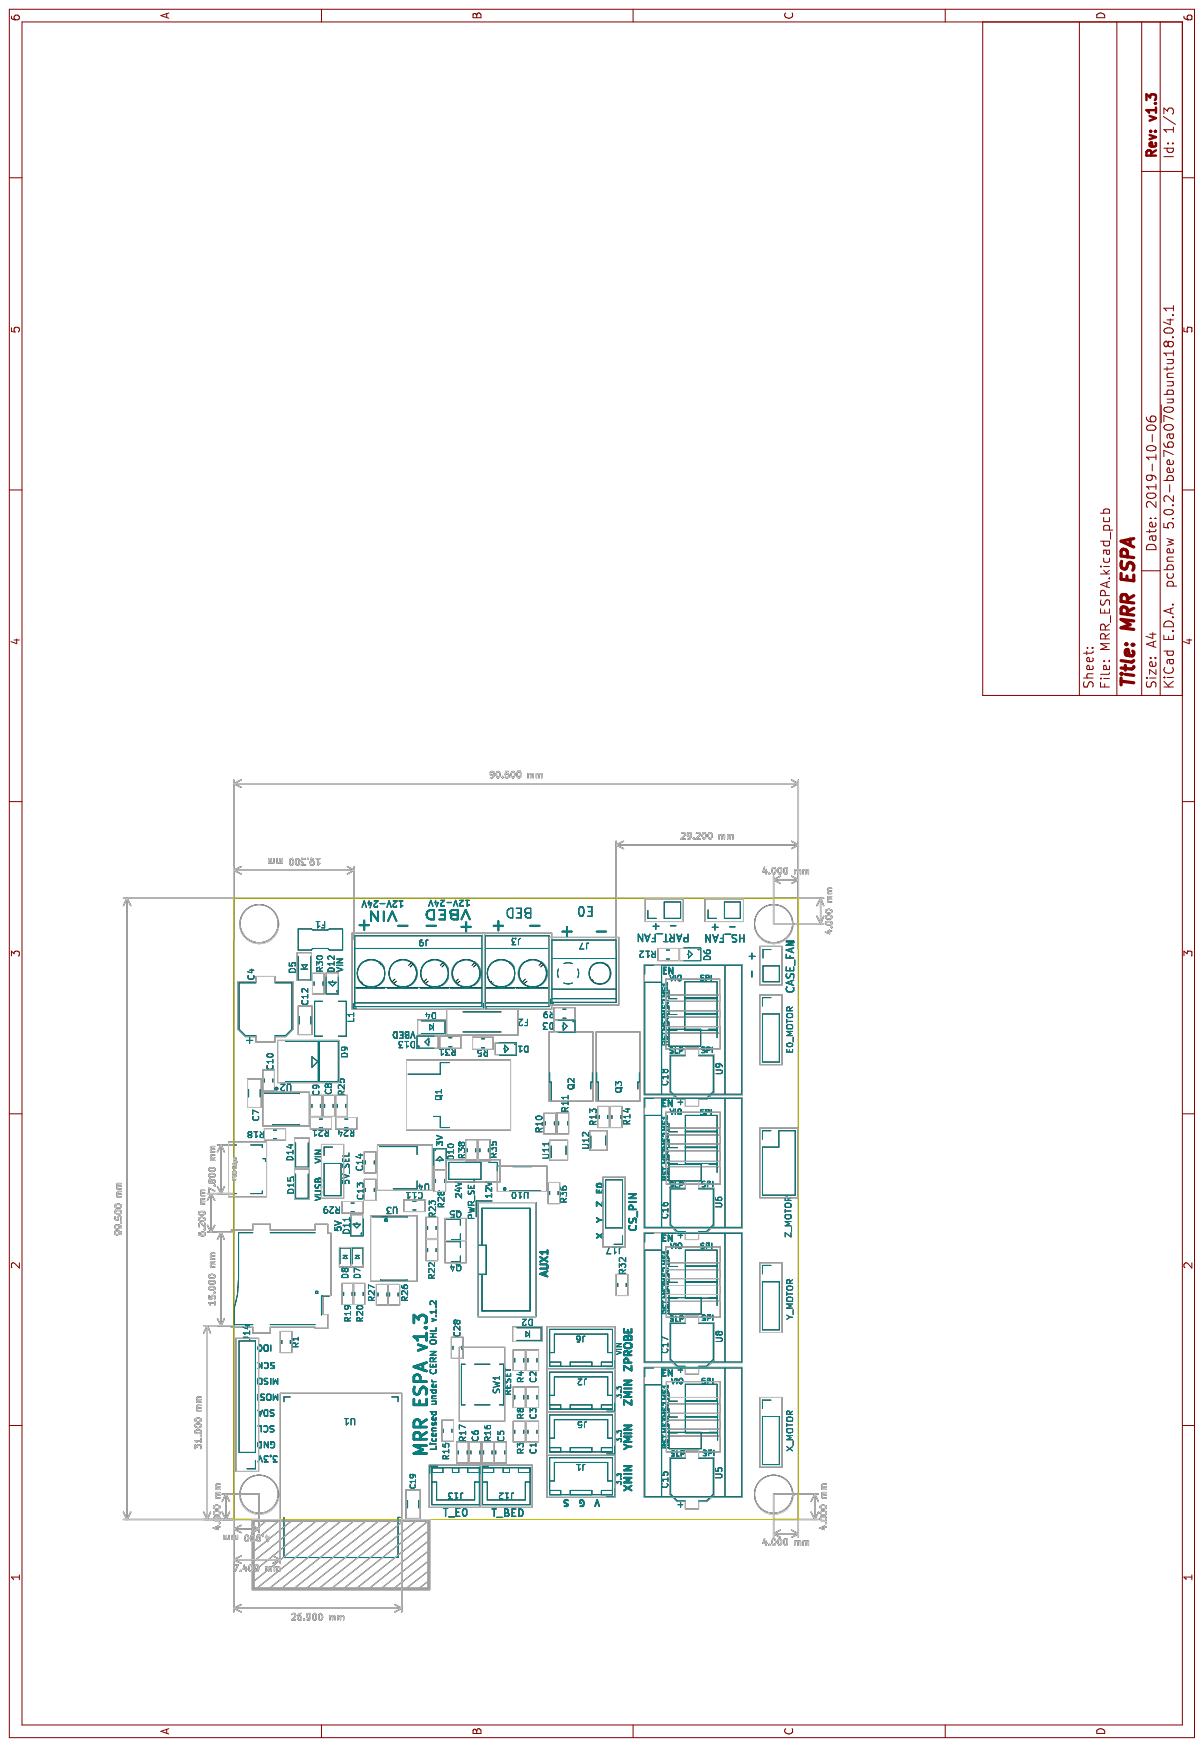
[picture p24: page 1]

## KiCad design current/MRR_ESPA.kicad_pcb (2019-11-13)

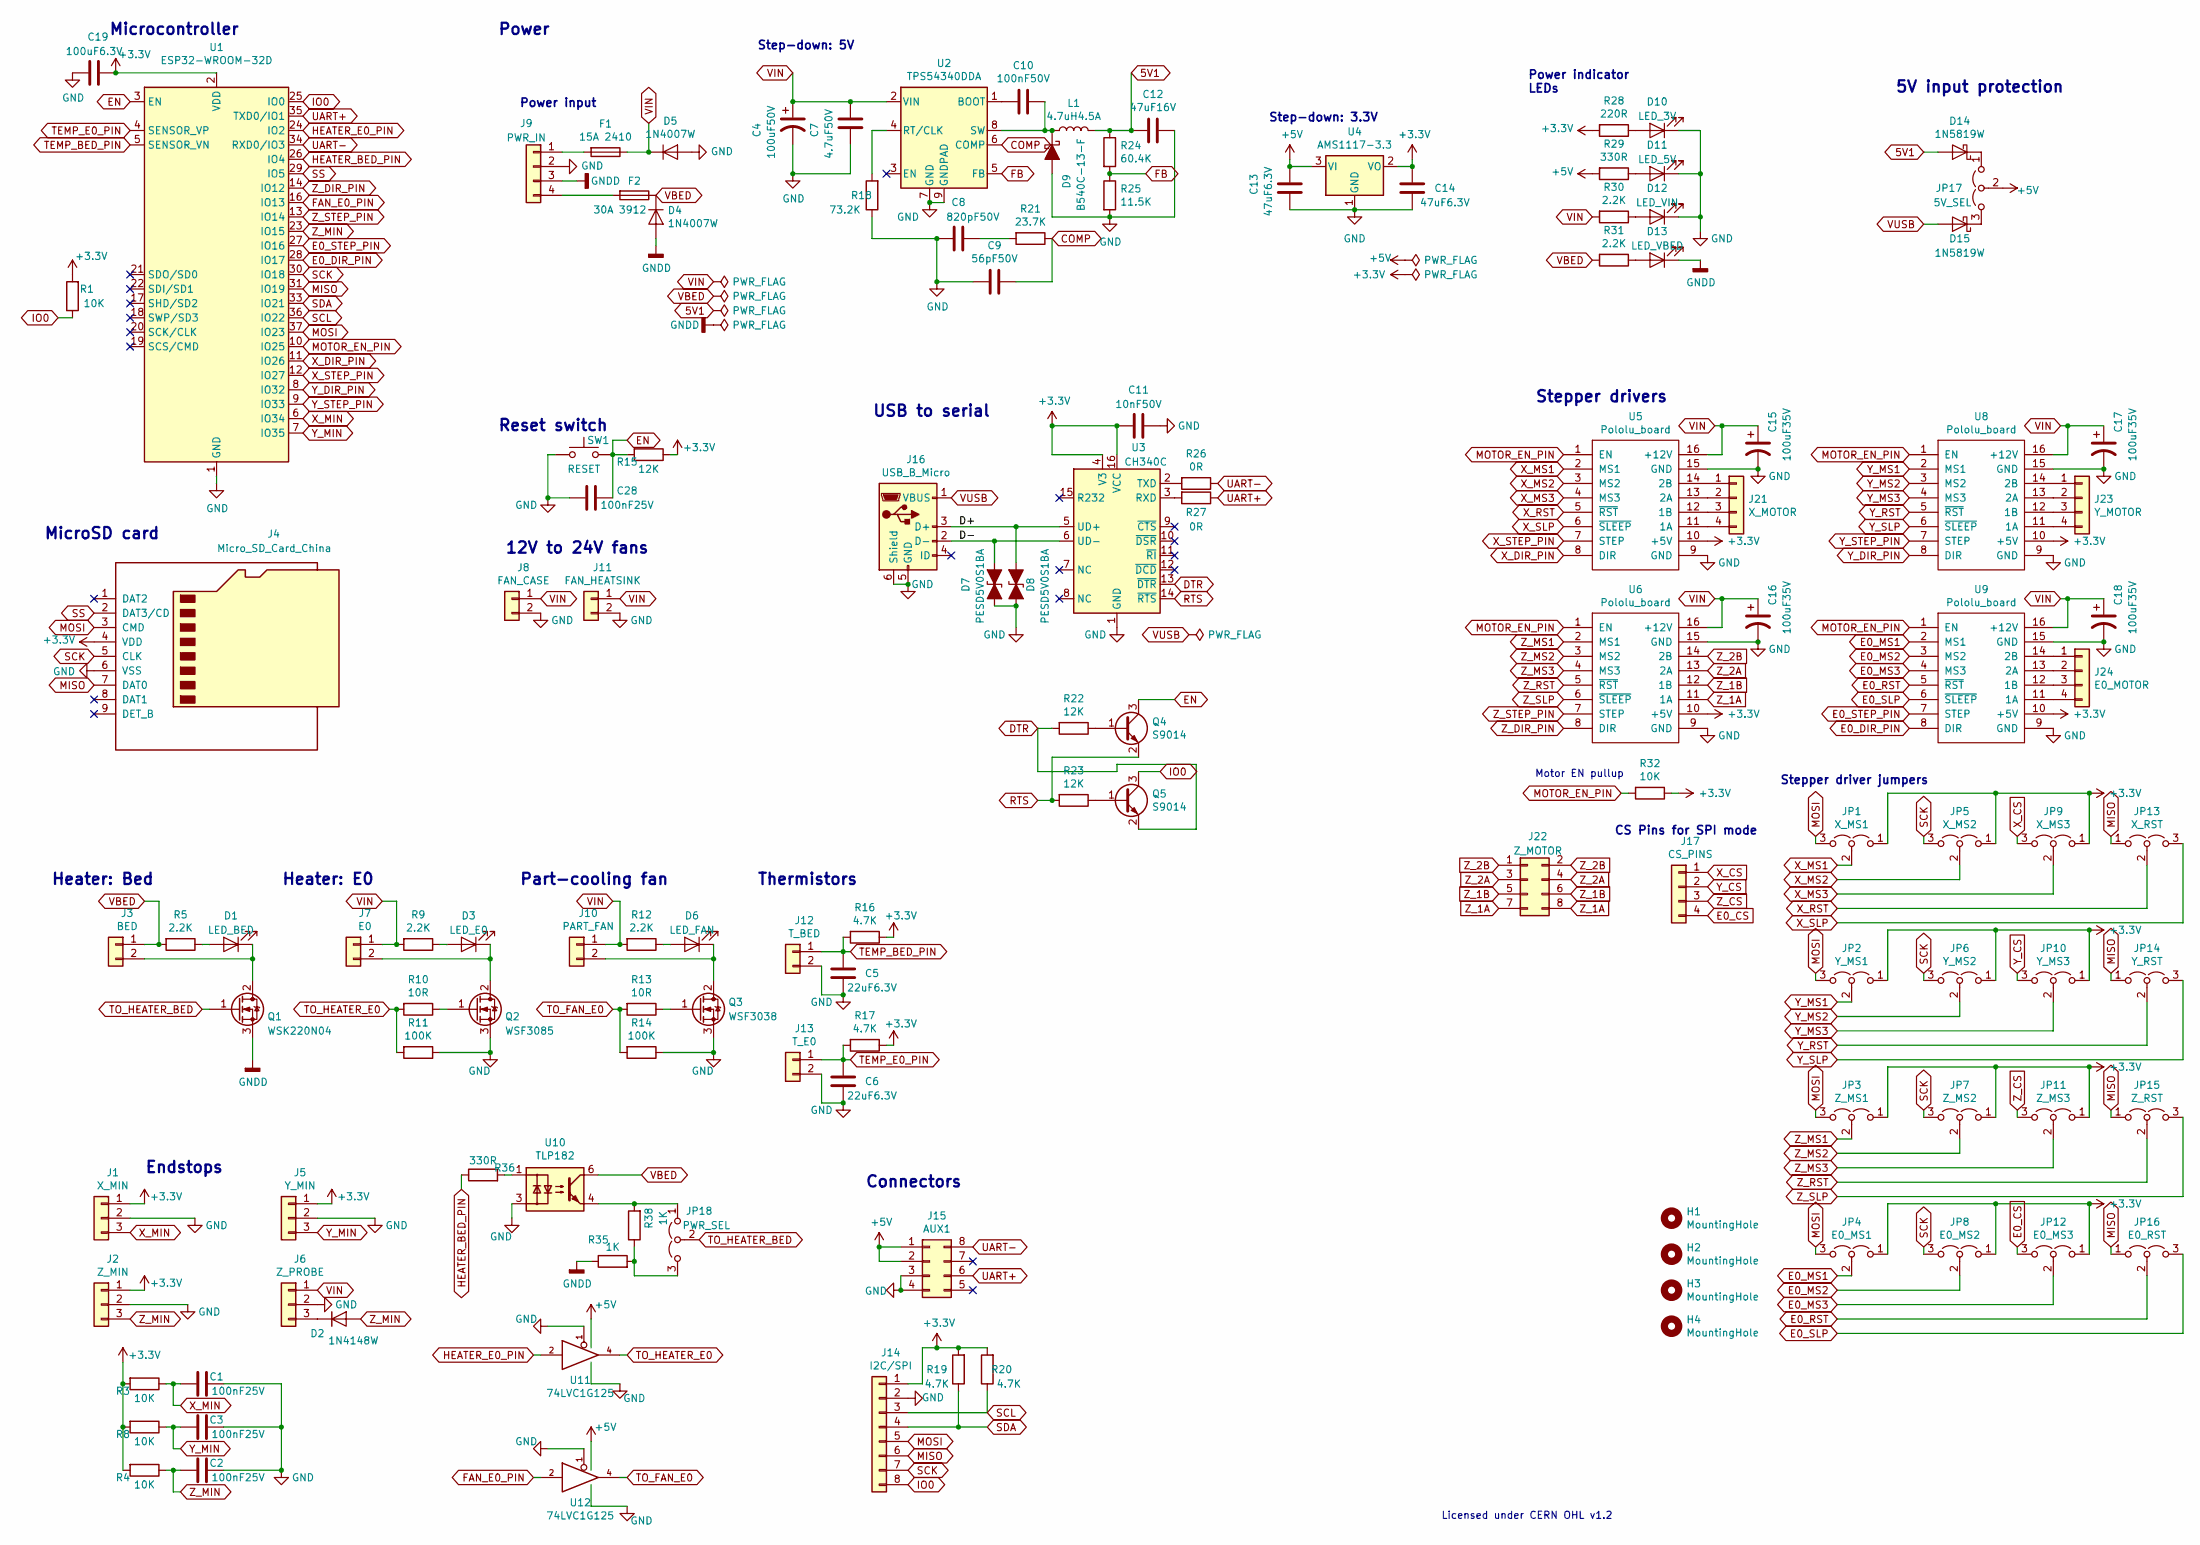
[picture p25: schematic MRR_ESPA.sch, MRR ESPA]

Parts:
C1, C2, C3, C28: 100nF25V; C_0805_2012Metric; Mfg part no. 0805B104K250; LCSC Part Number C128353
C4: 100uF50V; CP_Elec_8x10; Mfg part no. VEJ101M1HTR-0810; LCSC Part Number C176665
C5, C6: 22uF6.3V; C_0805_2012Metric; Mfg part no. CL21A226MQQNNNE; LCSC Part Number C5674
C7: 4.7uF50V; C_1206_3216Metric; Mfg part no. CL31B475KBHNFNE; LCSC Part Number C307575
C8: 820pF50V; C_0805_2012Metric; Mfg part no. 0805B821K500CT; LCSC Part Number C152862
C9: 56pF50V; C_0805_2012Metric; Mfg part no. 0805N560J500CT; LCSC Part Number C296102
C10: 100nF50V; C_0805_2012Metric; Mfg part no. GCM21BR71H104KA37L; LCSC Part Number C161260
C11: 10nF50V; C_0805_2012Metric; Mfg part no. 0805B103K500NT; LCSC Part Number C52278
C12: 47uF16V; C_1206_3216Metric; Mfg part no. LMK316BJ476ML-T; LCSC Part Number C92821
C13, C14: 47uF6.3V; C_0805_2012Metric; Mfg part no. JMK212BJ476MG-T; LCSC Part Number C87159
C15, C16, C17, C18: 100uF35V; CP_Elec_6.3x7.7; Mfg part no. CS1V101M-CRE77; LCSC Part Number C97811
C19: 100uF6.3V; C_1206_3216Metric; Mfg part no. CL31A107MQHNNNE; LCSC Part Number C15008
D1: LED_BED; LED_0805; Mfg part no. 17-21SURC/S530-A3/TR8; LCSC Part Number C72037
D2: 1N4148W; D_SOD-123; Mfg part no. 1N4148W; LCSC Part Number C81598
D3: LED_E0; LED_0805; Mfg part no. 17-21SURC/S530-A3/TR8; LCSC Part Number C72037
D4, D5: 1N4007W; D_SOD-123F; Mfg part no. 1N4007W; LCSC Part Number C108803
D6: LED_FAN; LED_0805; Mfg part no. 17-21SURC/S530-A3/TR8; LCSC Part Number C72037
D7, D8: PESD5V0S1BA; D_SOD-323; Mfg part no. PESD5V0S1BA,115; LCSC Part Number C19224
D9: B540C-13-F; D_SMC; Mfg part no. B540C-13-F; LCSC Part Number C72264
D10: LED_3V; LED_0805; Mfg part no. 17-21SYGC/S530-E2/TR8; LCSC Part Number C73548
D11: LED_5V; LED_0805; Mfg part no. 17-21SYGC/S530-E2/TR8; LCSC Part Number C73548
D12: LED_VIN; LED_0805; Mfg part no. 17-21/BHC-XL2M2TY/3T; LCSC Part Number C72035
D13: LED_VBED; LED_0805; Mfg part no. 17-21/BHC-XL2M2TY/3T; LCSC Part Number C72035
D14, D15: 1N5819W; D_SOD-123; Mfg part no. 1N5819W; LCSC Part Number C169540
F1: 15A 2410; Littelfuse_0451; Mfg part no. 0451015.MRL; LCSC Part Number C44480
F2: 30A 3912; Littelfuse_456; Mfg part no. 0456030.ER; LCSC Part Number C187558
H1, H2, H3, H4: MountingHole; MountingHole_3.2mm_M3_DIN965
J1: X_MIN; JST_XH_B03B-XH-A_1x03_P2.50mm_Vertical; Mfg part no. B3B-XH-A(LF)(SN); LCSC Part Number C144394
J2: Z_MIN; JST_XH_B03B-XH-A_1x03_P2.50mm_Vertical; Mfg part no. B3B-XH-A(LF)(SN); LCSC Part Number C144394
J3: BED; TerminalBlock_Phoenix_MKDS-3-2-5.08_1x02_P5.08mm_Horizontal; Mfg part no. MKDS3/2-5.08; LCSC Part Number C89120
J4: Micro_SD_Card_China; Conn_uSDcard; Mfg part no. TF-15×15; LCSC Part Number C111196
J5: Y_MIN; JST_XH_B03B-XH-A_1x03_P2.50mm_Vertical; Mfg part no. B3B-XH-A(LF)(SN); LCSC Part Number C144394
J6: Z_PROBE; JST_XH_B03B-XH-A_1x03_P2.50mm_Vertical; Mfg part no. B3B-XH-A(LF)(SN); LCSC Part Number C144394
J7: E0; TerminalBlock_Phoenix_MKDS-1,5-2-5.08_1x02_P5.08mm_Horizont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; Mfg part no. MKDSN1.5/2-5.08; LCSC Part Number C91153
J8: FAN_CASE; PinHeader_1x02_P2.54mm_Vertical; Mfg part no. C124375; LCSC Part Number C124375
J9: PWR_IN; TerminalBlock_Phoenix_MKDS-3-4-5.08_1x04_P5.08mm_Horizontal; Mfg part no. MKDS3/4-5.08; LCSC Part Number C90087
J10: PART_FAN; PinHeader_1x02_P2.54mm_Vertical; Mfg part no. C124375; LCSC Part Number C124375
J11: FAN_HEATSINK; PinHeader_1x02_P2.54mm_Vertical; Mfg part no. C124375; LCSC Part Number C124375
J12: T_BED; JST_XH_B02B-XH-A_1x02_P2.50mm_Vertical; Mfg part no. B2B-XH-A(LF)(SN); LCSC Part Number C158012
J13: T_E0; JST_XH_B02B-XH-A_1x02_P2.50mm_Vertical; Mfg part no. B2B-XH-A(LF)(SN); LCSC Part Number C158012
J14: I2C/SPI; PinHeader_1x08_P2.54mm_Vertical; Mfg part no. C124381; LCSC Part Number C124381
J15: AUX1; IDC-Header_2x04_P2.54mm_Vertical; Mfg part no. C9135; LCSC Part Number C9135
J16: USB_B_Micro; USB_Micro-B_Molex-105017-0001; Mfg part no. 105017-0001; LCSC Part Number C136000
J17: CS_PINS; PinHeader_1x04_P2.54mm_Vertical; Mfg part no. C124378; LCSC Part Number C124378
J21: X_MOTOR; PinHeader_1x04_P2.54mm_Vertical; Mfg part no. C124378; LCSC Part Number C124378
J22: Z_MOTOR; PinHeader_2x04_P2.54mm_Vertical; Mfg part no. C124386; LCSC Part Number C124386
J23: Y_MOTOR; PinHeader_1x04_P2.54mm_Vertical; Mfg part no. C124378; LCSC Part Number C124378
J24: E0_MOTOR; PinHeader_1x04_P2.54mm_Vertical; Mfg part no. C124378; LCSC Part Number C124378
JP1: X_MS1; PinHeader_1x03_P2.54mm_Vertical; Mfg part no. C124376; LCSC Part Number C124376
JP2: Y_MS1; PinHeader_1x03_P2.54mm_Vertical; Mfg part no. C124376; LCSC Part Number C124376
JP3: Z_MS1; PinHeader_1x03_P2.54mm_Vertical; Mfg part no. C124376; LCSC Part Number C124376
JP4: E0_MS1; PinHeader_1x03_P2.54mm_Vertical; Mfg part no. C124376; LCSC Part Number C124376
JP5: X_MS2; PinHeader_1x03_P2.54mm_Vertical; Mfg part no. C124376; LCSC Part Number C124376
JP6: Y_MS2; PinHeader_1x03_P2.54mm_Vertical; Mfg part no. C124376; LCSC Part Number C124376
JP7: Z_MS2; PinHeader_1x03_P2.54mm_Vertical; Mfg part no. C124376; LCSC Part Number C124376
JP8: E0_MS2; PinHeader_1x03_P2.54mm_Vertical; Mfg part no. C124376; LCSC Part Number C124376
JP9: X_MS3; PinHeader_1x03_P2.54mm_Vertical; Mfg part no. C124376; LCSC Part Number C124376
JP10: Y_MS3; PinHeader_1x03_P2.54mm_Vertical; Mfg part no. C124376; LCSC Part Number C124376
JP11: Z_MS3; PinHeader_1x03_P2.54mm_Vertical; Mfg part no. C124376; LCSC Part Number C124376
JP12: E0_MS3; PinHeader_1x03_P2.54mm_Vertical; Mfg part no. C124376; LCSC Part Number C124376
JP13: X_RST; PinHeader_1x03_P2.54mm_Vertical; Mfg part no. C124376; LCSC Part Number C124376
JP14: Y_RST; PinHeader_1x03_P2.54mm_Vertical; Mfg part no. C124376; LCSC Part Number C124376
JP15: Z_RST; PinHeader_1x03_P2.54mm_Vertical; Mfg part no. C124376; LCSC Part Number C124376
JP16: E0_RST; PinHeader_1x03_P2.54mm_Vertical; Mfg part no. C124376; LCSC Part Number C124376
JP17: 5V_SEL; PinHeader_1x03_P2.54mm_Vertical; Mfg part no. C124376; LCSC Part Number C124376
JP18: PWR_SEL; PinHeader_1x03_P2.54mm_Vertical; Mfg part no. C124376; LCSC Part Number C124376
L1: 4.7uH4.5A; SMMS0530; Mfg part no. SMMS0530-4R7M; LCSC Part Number C181722
Q1: WSK220N04; TO-263-2; Mfg part no. WSK220N04; LCSC Part Number C148446
Q2: WSF3085; TO-252-2; Mfg part no. WSF3085; LCSC Part Number C148428
Q3: WSF3038; TO-252-2; Mfg part no. WSF3038; LCSC Part Number C148426
Q4, Q5: S9014; SOT-23; Mfg part no. S9014; LCSC Part Number C181164
R1, R3, R4, R8, R32: 10K; R_0805_2012Metric; Mfg part no. 0805W8F2201T5E; LCSC Part Number C38522
R5, R9, R12, R30, R31: 2.2K; R_0805_2012Metric; Mfg part no. 0805W8F2201T5E; LCSC Part Number C17520
R10, R13: 10R; R_0805_2012Metric; Mfg part no. 0805W8F100JT5E; LCSC Part Number C17415
R11, R14: 100K; R_0805_2012Metric; Mfg part no. 0805W8F1003T5E; LCSC Part Number C149504
R15, R22, R23: 12K; R_0805_2012Metric; Mfg part no. 0805W8F1202T5E; LCSC Part Number C17444
R16, R17, R19, R20: 4.7K; R_0805_2012Metric; Mfg part no. 0805W8F4701T5E; LCSC Part Number C17673
R18: 73.2K; R_0805_2012Metric; Mfg part no. WR08X7322FTL; LCSC Part Number C170958
R21: 23.7K; R_0805_2012Metric; Mfg part no. WR08X2372FTL; LCSC Part Number C170848
R24: 60.4K; R_0805_2012Metric; Mfg part no. RC0805FR-0760K4L; LCSC Part Number C273994
R25: 11.5K; R_0805_2012Metric; Mfg part no. 0805W8F1152T5E; LCSC Part Number C17418
R26, R27: 0R; R_0805_2012Metric; Mfg part no. 0805W8F0000T5E; LCSC Part Number C17477
R28: 220R; R_0805_2012Metric; Mfg part no. 0805W8F2200T5E; LCSC Part Number C17557
R29, R36: 330R; R_0805_2012Metric; Mfg part no. 0805W8F3300T5E; LCSC Part Number C17630
R35, R38: 1K; R_0805_2012Metric; Mfg part no. 0805W8F1001T5E; LCSC Part Number C17513
SW1: RESET; 6x6mmTactileSwitch; Mfg part no. K2-6639SP-C4SC-04; LCSC Part Number C83206
U1: ESP32-WROOM-32D; ESP32-WROOM-32; Mfg part no. ESP32-WROOM-32; LCSC Part Number C95209
U2: TPS54340DDA; TI_SO-PowerPAD-8_ThermalVias; Mfg part no. TPS54340DDAR; LCSC Part Number C45886
U3: CH340C; SOIC-16_3.9x9.9mm_P1.27mm; Mfg part no. CH340C; LCSC Part Number C84681
U4: AMS1117-3.3; SOT-223-3_TabPin2; Mfg part no. AMS1117-3.3; LCSC Part Number C6186
U5, U6, U8, U9: Pololu_board; Pololu_Breakout-16_15.2x20.3mm; Mfg part no. x2; LCSC Part Number C27438
U10: TLP182; MFSOP6-4_4.4x3.6mm_P1.27mm; Mfg part no. TLP182(GB-TPL,E; LCSC Part Number C96457
U11, U12: 74LVC1G125; SOT-353_SC-70-5; Mfg part no. 74LVC1G125GW,125; LCSC Part Number C12519

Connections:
5V1: C12.2, D14.2 (A), L1.2, R24.1
+3V3: C11.2, C14.1, C19.1, J1.1, J2.1, J4.4 (VDD), J5.1, J14.1, JP1.1 (A), JP2.1 (A), JP3.1 (A), JP4.1 (A), JP5.1 (A), JP6.1 (A), JP7.1 (A), JP8.1 (A), JP9.1 (A), JP10.1 (A), JP11.1 (A), JP12.1 (A), R1.2, R3.2, R4.2, R8.2, R15.1, R16.1, R17.1, R19.2, R20.2, R28.2, R32.1, U1.2 (VDD), U3.4 (V3), U3.16 (VCC), U4.2 (VO), U5.10 (+5V), U6.10 (+5V), U8.10 (+5V), U9.10 (+5V)
+5V: C13.1, J15.1, J15.2, JP17.2 (C), R29.2, U4.3 (VI), U11.5 (VCC), U12.5 (VCC)
/D+: D8.1 (A1), J16.3 (D+), U3.5 (UD+)
/D-: D7.1 (A1), J16.2 (D-), U3.6 (UD-)
COMP: C9.1, R21.1, U2.6 (COMP)
DTR: Q5.2 (E), R22.2, U3.13 (~DTR)
E0_CS: J17.4, JP12.3 (B)
E0_DIR_PIN: U1.28 (IO17), U9.8 (DIR)
E0_MS1: JP4.2 (C), U9.2 (MS1)
E0_MS2: JP8.2 (C), U9.3 (MS2)
E0_MS3: JP12.2 (C), U9.4 (MS3)
E0_RST: JP16.2 (C), U9.5 (~RST)
E0_SLP: JP16.3 (B), U9.6 (~SLEEP)
E0_STEP_PIN: U1.27 (IO16), U9.7 (STEP)
EN: C28.1, Q4.3 (C), R15.2, SW1.2, U1.3 (EN)
FAN_E0_PIN: U1.16 (IO13), U12.2
FB: R24.2, R25.1, U2.5 (FB)
GND: C1.1, C2.1, C3.1, C4.2, C5.1, C6.1, C7.1, C8.2, C9.2, C11.1, C12.1, C13.2, C14.2, C15.2, C16.2, C17.2, C18.2, C19.2, C28.2, D5.2 (A), D7.2 (A2), D8.2 (A2), D9.2 (A), D10.1 (K), D11.1 (K), D12.1 (K), J1.2, J2.2, J4.6 (VSS), J5.2, J6.2, J8.2, J9.2, J11.2, J12.2, J13.2, J14.2, J15.3, J15.4, J16.5 (GND), J16.6 (Shield), Q2.3 (S), Q3.3 (S), R11.1, R14.1, R18.1, R25.2, SW1.1, U1.1 (GND), U1.15 (GND), U1.38 (GND), U1.39, U2.7 (GND), U2.9 (GNDPAD), U3.1 (GND), U4.1 (GND), U5.9 (GND), U5.15 (GND), U6.9 (GND), U6.15 (GND), U8.9 (GND), U8.15 (GND), U9.9 (GND), U9.15 (GND), U10.3, U11.1, U11.3 (GND), U12.1, U12.3 (GND)
GNDD: D4.2 (A), D13.1 (K), J9.3, Q1.3 (S), R35.1
HEATER_BED_PIN: R36.1, U1.26 (IO4)
HEATER_E0_PIN: U1.24 (IO2), U11.2
IO0: J14.8, Q5.3 (C), R1.1, U1.25 (IO0)
MISO: J4.7 (DAT0), J14.6, JP13.1 (A), JP14.1 (A), JP15.1 (A), JP16.1 (A), U1.31 (IO19)
MOSI: J4.3 (CMD), J14.5, JP1.3 (B), JP2.3 (B), JP3.3 (B), JP4.3 (B), U1.37 (IO23)
MOTOR_EN_PIN: R32.2, U1.10 (IO25), U5.1 (EN), U6.1 (EN), U8.1 (EN), U9.1 (EN)
unnamed: C8.1, R21.2
unnamed: C10.1, D9.1 (K), L1.1, U2.8 (SW)
unnamed: C10.2, U2.1 (BOOT)
unnamed: D1.1 (K), J3.2, Q1.2 (D)
unnamed: D1.2 (A), R5.1
unnamed: D2.1 (K), J6.3
unnamed: D3.1 (K), J7.2, Q2.2 (D)
unnamed: D3.2 (A), R9.1
unnamed: D6.1 (K), J10.2, Q3.2 (D)
unnamed: D6.2 (A), R12.1
unnamed: D10.2 (A), R28.1
unnamed: D11.2 (A), R29.1
unnamed: D12.2 (A), R30.1
unnamed: D13.2 (A), R31.1
unnamed: D14.1 (K), JP17.1 (A)
unnamed: D15.1 (K), JP17.3 (B)
unnamed: F1.2, J9.1
unnamed: F2.2, J9.4
unnamed: J21.1, U5.14 (2B)
unnamed: J21.2, U5.13 (2A)
unnamed: J21.3, U5.12 (1B)
unnamed: J21.4, U5.11 (1A)
unnamed: J23.1, U8.14 (2B)
unnamed: J23.2, U8.13 (2A)
unnamed: J23.3, U8.12 (1B)
unnamed: J23.4, U8.11 (1A)
unnamed: J24.1, U9.14 (2B)
unnamed: J24.2, U9.13 (2A)
unnamed: J24.3, U9.12 (1B)
unnamed: J24.4, U9.11 (1A)
unnamed: JP18.1 (A), R38.2, U10.4
unnamed: JP18.3 (B), R35.2, R38.1
unnamed: Q2.1 (G), R10.1
unnamed: Q3.1 (G), R13.1
unnamed: Q4.1 (B), R22.1
unnamed: Q5.1 (B), R23.1
unnamed: R18.2, U2.4 (RT/CLK)
unnamed: R26.2, U3.2 (TXD)
unnamed: R27.2, U3.3 (RXD)
unnamed: R36.2, U10.1
RTS: Q4.2 (E), R23.2, U3.14 (~RTS)
SCK: J4.5 (CLK), J14.7, JP5.3 (B), JP6.3 (B), JP7.3 (B), JP8.3 (B), U1.30 (IO18)
SCL: J14.3, R20.1, U1.36 (IO22)
SDA: J14.4, R19.1, U1.33 (IO21)
SS: J4.2 (DAT3/CD), U1.29 (IO5)
TEMP_BED_PIN: C5.2, J12.1, R16.2, U1.5 (SENSOR_VN)
TEMP_E0_PIN: C6.2, J13.1, R17.2, U1.4 (SENSOR_VP)
TO_FAN_E0: R13.2, R14.2, U12.4
TO_HEATER_BED: JP18.2 (C), Q1.1 (G)
TO_HEATER_E0: R10.2, R11.2, U11.4
UART+: J15.6, R27.1, U1.35 (TXD0/IO1)
UART-: J15.8, R26.1, U1.34 (RXD0/IO3)
VBED: D4.1 (K), F2.1, J3.1, R5.2, R31.2, U10.6
VIN: C4.1, C7.2, C15.1, C16.1, C17.1, C18.1, D5.1 (K), F1.1, J6.1, J7.1, J8.1, J10.1, J11.1, R9.2, R12.2, R30.2, U2.2 (VIN), U5.16 (+12V), U6.16 (+12V), U8.16 (+12V), U9.16 (+12V)
VUSB: D15.2 (A), J16.1 (VBUS)
X_CS: J17.1, JP9.3 (B)
X_DIR_PIN: U1.11 (IO26), U5.8 (DIR)
X_MIN: C1.2, J1.3, R3.1, U1.6 (IO34)
X_MS1: JP1.2 (C), U5.2 (MS1)
X_MS2: JP5.2 (C), U5.3 (MS2)
X_MS3: JP9.2 (C), U5.4 (MS3)
X_RST: JP13.2 (C), U5.5 (~RST)
X_SLP: JP13.3 (B), U5.6 (~SLEEP)
X_STEP_PIN: U1.12 (IO27), U5.7 (STEP)
Y_CS: J17.2, JP10.3 (B)
Y_DIR_PIN: U1.8 (IO32), U8.8 (DIR)
Y_MIN: C3.2, J5.3, R8.1, U1.7 (IO35)
Y_MS1: JP2.2 (C), U8.2 (MS1)
Y_MS2: JP6.2 (C), U8.3 (MS2)
Y_MS3: JP10.2 (C), U8.4 (MS3)
Y_RST: JP14.2 (C), U8.5 (~RST)
Y_SLP: JP14.3 (B), U8.6 (~SLEEP)
Y_STEP_PIN: U1.9 (IO33), U8.7 (STEP)
Z_1A: J22.7, J22.8, U6.11 (1A)
Z_1B: J22.5, J22.6, U6.12 (1B)
Z_2A: J22.3, J22.4, U6.13 (2A)
Z_2B: J22.1, J22.2, U6.14 (2B)
Z_CS: J17.3, JP11.3 (B)
Z_DIR_PIN: U1.14 (IO12), U6.8 (DIR)
Z_MIN: C2.2, D2.2 (A), J2.3, R4.1, U1.23 (IO15)
Z_MS1: JP3.2 (C), U6.2 (MS1)
Z_MS2: JP7.2 (C), U6.3 (MS2)
Z_MS3: JP11.2 (C), U6.4 (MS3)
Z_RST: JP15.2 (C), U6.5 (~RST)
Z_SLP: JP15.3 (B), U6.6 (~SLEEP)
Z_STEP_PIN: U1.13 (IO14), U6.7 (STEP)

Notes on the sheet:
Microcontroller
MicroSD card
Power
Step-down: 5V
Step-down: 3.3V
Power indicator LEDs
Power input
USB to serial
5V input protection
Heater: Bed
Heater: E0
Part-cooling fan
Motor EN pullup
Stepper drivers
12V to 24V fans
Thermistors
Endstops
Reset switch
Connectors
Stepper driver jumpers
Licensed under CERN OHL v1.2
CS Pins for SPI mode

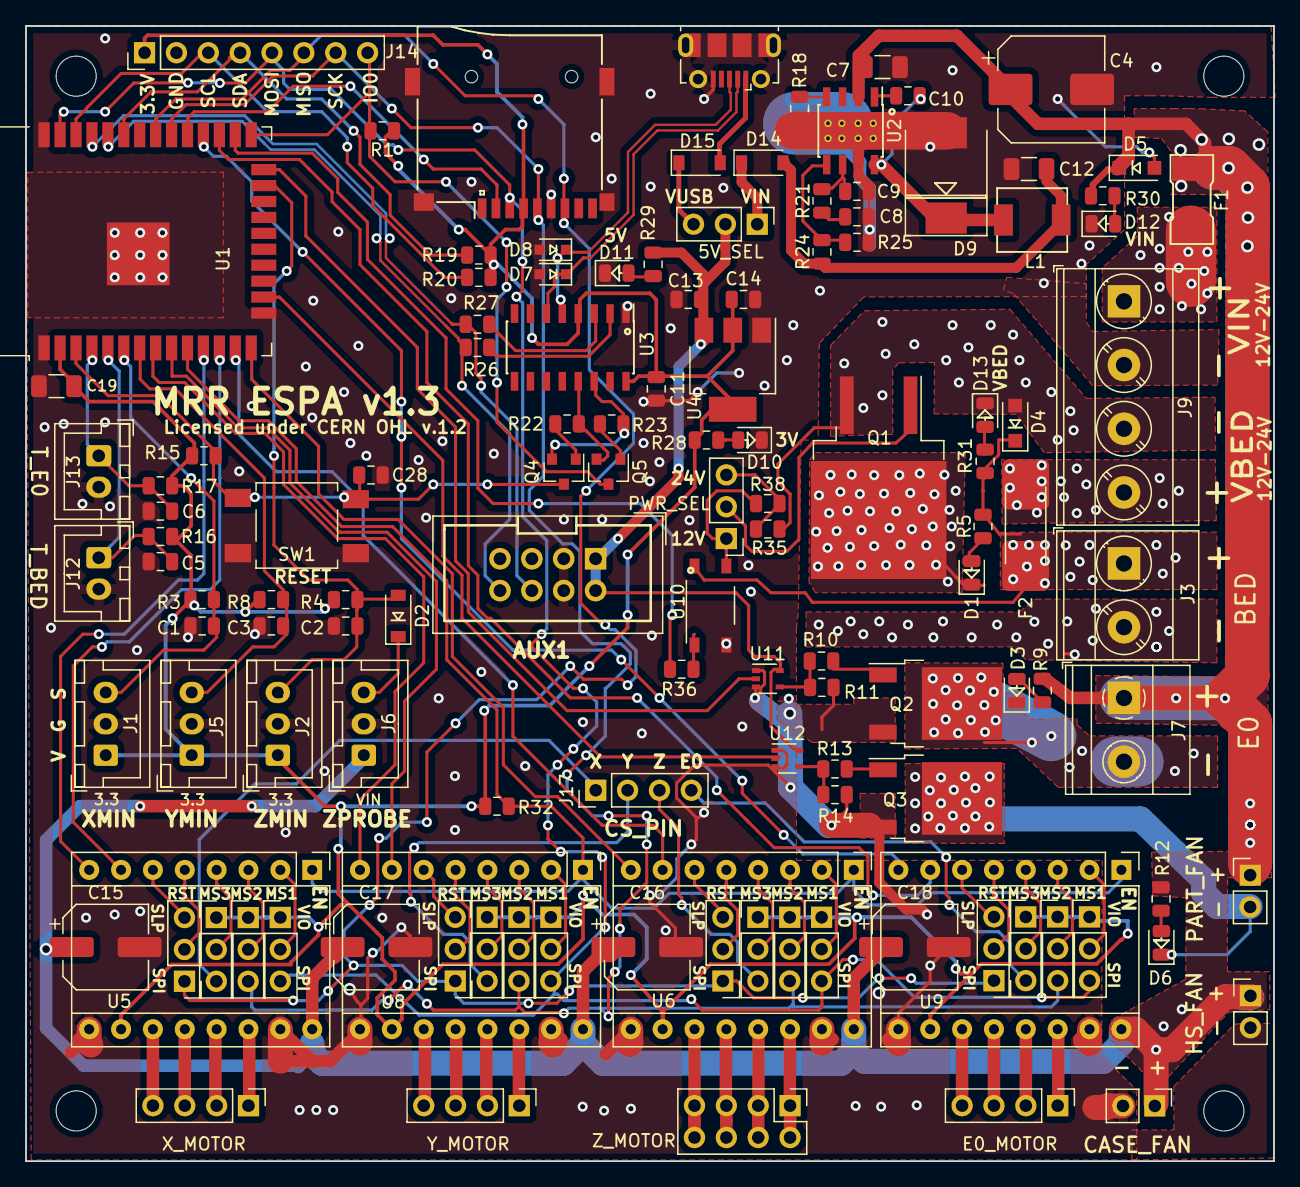
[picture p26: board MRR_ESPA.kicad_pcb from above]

Board: 2 copper layers, 99.5 x 90.5 mm, 130 parts (0 on the bottom side), 112 nets.

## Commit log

2019-06-23 Added firmware folder
    [abortabl.g, babyzdn.g, babyzup.g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]
2019-09-09 Added v1.2
    [MRR_ESPA-B.Cu.gbl, MRR_ESPA-B.Mask.gbs, MRR_ESPA-B.Paste.gbp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]
2019-10-24 Added v1.3 files
    [MRR_ESPA-B.Cu.gbl, MRR_ESPA-B.Mask.gbs, MRR_ESPA-B.Paste.gbp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]
2019-10-25 Added cases
    [40mm_fan_cover.stl, 80mm_fan_cover.stl, ESPA_basic_bottom.stl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]
2019-11-13 Added dimensions drawing
    [MRR_ESPA.kicad_pcb]
2019-12-09 Changed AUX1 connector symbol
    [MRR_ESPA.sch]
